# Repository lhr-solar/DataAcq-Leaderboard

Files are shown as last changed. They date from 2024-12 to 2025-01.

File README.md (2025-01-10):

# DataAcquisitionLeaderPCB

This PCB is designed for our solar vehicle to collect electrical and mechanical sensor data and transmit it wirelessly via LTE for real-time access. It also includes a GPS module for location tracking and an RF module as a backup communication system.

## LED Descriptions

LTE LEDs:

* HB (D7): Heartbeat.
  * Blinking = Our code is running on module.
* RSSI (D5): Received Singal Strength Integrity.
  * PWM based on strength (brighter = better).
* CONN (D4): Connection Indicator.
  * On, solid = Not connected.
  * 1/2 sec period blink = Last transmit failed.
  * 1 sec blink period = Normal operation.
* ON (D6): On.
  * On = Module is on.

RF LEDs:

* COM (D1): Commissioning (associate) status.
  * Blinking = Device is powered and operating properly.
  * Off = Device is alseep.
  * Note: blinks with certain patterns depending on number of RF_COM button presses (see datasheet).
* ON (D2): On.
  * On = Module is on.
* RSSI (D3): Received Singal Strength Integrity.
  * PWM based on strength (brighter = better).

GPS LED:

* NFX (D8): Negative 3D Fix.
  * Blinking (2 sec period) = Searching for satellites, no position fix.
  * Off = Acquired satellite signal.

## Testpoint Descriptions

LTE Testpoints:

* UART5 (J3)
  * Pin 3 TX = Transmit
  * Pin 2 RX = Receive
  * Pin 1 NR = Negative Reset (Note: this is not a UART singal, it is the module NRESET singal)

* Test Trace (J4)
  * Provides access to 4 pins (traces) to help in debugging code on the LTE module.

RF Testpoints:

* UART2 (J2)
  * Pin 3 TX = Transmit
  * Pin 2 RX = Receive
  * Pin 1 NR = Negative Reset (Note: this is not a UART singal, it is the module NRESET singal)

GPS Testpoints:

* I2C (J5)
  * Pin 3 SDA = Serial Data
  * Pin 2 SCL = Serial Clock
  * Pin 1 NR = Negative Reset (Note: this is not a I2C singal, it is the module NRESET singal)

## Pushbutton Descriptions

LTE_RESET: When pressed LTE module resets.
GPS_RESET: When pressed GPS module resets.
RF_RESET: When pressed RF module resets.
RF_COM: RF Commissioning button (see datasheet).

## PCB

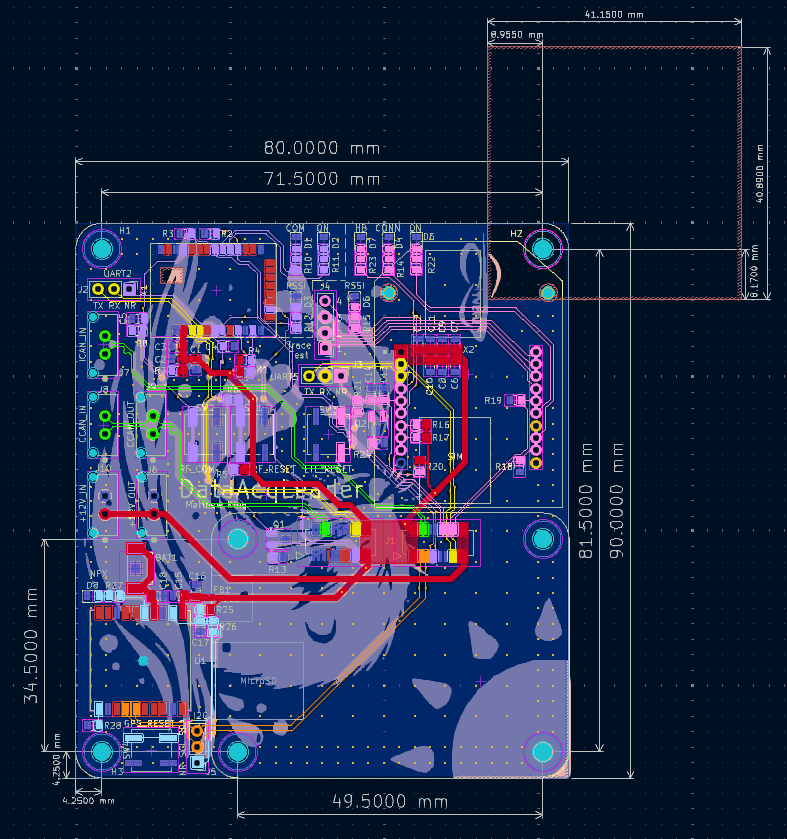
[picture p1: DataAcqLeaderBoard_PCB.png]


## Schematic

[PDF](DataAcqLeaderBoard_Schematic.pdf)

## BOM

[BOM](DataAcqLeaderBoard/bom/bom.csv)
[IBOM](DataAcqLeaderBoard/bom/ibom.html)
[Mouser Cart](https://www.mouser.com/ProjectManager/ProjectDetail.aspx?AccessID=583e28cb45)

Cart does not include: 

  - [GPS Ferite Bead](https://www.digikey.com/en/products/detail/pulse-electronics/GMLB-100505-0600A-N8/12417638)
  - [GPS Module]( https://www.adafruit.com/product/790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)
  - [Digi XBee LTE Module](https://www.digi.com/products/embedded-systems/digi-xbee/cellular-modems/digi-xbee-3-global-lte-cat-4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 )
  - [Digi XBee RF Module](https://www.digi.com/products/embedded-systems/digi-xbee/rf-modules/sub-1-ghz-rf-modules/digi-xbee-xr-900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)

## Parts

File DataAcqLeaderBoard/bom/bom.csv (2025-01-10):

# | Reference | Value | Qty | Footprint | Datasheet | P/N | Mouser Part Number | Link | DNP
1 | BAT1 | ML414 | 1 | DataAcqLeaderBoard-Footprints:BAT_2994TR | https://www.mouser.com/ProductDetail/Keystone-Electronics/2994TR?qs=BMR1h6ig6pBQGK4xQ7FwKQ%3D%3D | 2994TR | 534-2994TR | https://www.mouser.com/ProductDetail/Keystone-Electronics/2994TR?qs=BMR1h6ig6pBQGK4xQ7FwKQ%3D%3D
2 | C1,C9 | 10u | 2 | Capacitor_SMD:C_0805_2012Metric | ~ | TCP0J106M8R | 755-TCP0J106M8R | https://www.mouser.com/ProductDetail/KYOCERA-AVX/TCP0J106M8R?qs=gmcn8Ik9O3HZ%252B34S5YYCCQ%3D%3D
3 | C2,C4,C5,C14,C15,C17,C18 | 1u | 7 | Capacitor_SMD:C_0805_2012Metric | ~ | C0805C105J4RAC7210 | 80-C0805C105J4RACLR | https://www.mouser.com/ProductDetail/KEMET/C0805C105J4RAC7210?qs=7zB%252BIQS%2FKOJG%252BUtduyFhHw%3D%3D
4 | C3 | 47p | 1 | Capacitor_SMD:C_0805_2012Metric | ~ | C0805C470F5GACTU | 80-C0805C470F5G | https://www.mouser.com/ProductDetail/KEMET/C0805C470F5GACTU?qs=fI854BrZEijgUEI6lxo0jA%3D%3D
5 | C6,C7,C8 | 100u | 3 | Capacitor_SMD:C_0805_2012Metric | ~ | TCTPL0G107M8R-V1 | 755-TCTPL0G107M8R-V1 | https://www.mouser.com/ProductDetail/KYOCERA-AVX/TCTPL0G107M8R-V1?qs=Y0Uzf4wQF3nuA76NpVN8fA%3D%3D
6 | C10,C13 | 10n | 2 | Capacitor_SMD:C_0805_2012Metric | ~ | C0805C103F8HACAUTO | 80-C0805C103F8HAUTO | https://www.mouser.com/ProductDetail/KEMET/C0805C103F8HACAUTO?qs=j%252B1pi9TdxUbLXPjCpdS2Hw%3D%3D
7 | C11 | 56p | 1 | Capacitor_SMD:C_0805_2012Metric | ~ | C0805C560FBGACTU | 80-C0805C560FBG | https://www.mouser.com/ProductDetail/KEMET/C0805C560FBGACTU?qs=7IaIRco65pnJB5L%2Foom%252BKQ%3D%3D
8 | C12 | 10p | 1 | Capacitor_SMD:C_0805_2012Metric | ~ | C0805C100F1GACTU | 80-C0805C100F1GACTU | https://www.mouser.com/ProductDetail/KEMET/C0805C100F1GACTU?qs=sowatxGsQyzyczo0gS71EQ%3D%3D
9 | C16 | 100n | 1 | Capacitor_SMD:C_0805_2012Metric | ~ | C0805C104M5RACTU | 80-C0805C104M5R | https://www.mouser.com/ProductDetail/KEMET/C0805C104M5RACTU?qs=VOOUd%252Bza08qHu13WgNByHQ%3D%3D
10 | D1,D2,D3,D4,D5,D6,D7,D8 | -- mixed values -- | 8 | LED_SMD:LED_0805_2012Metric |  | APTD2012LCGCK | 604-APTD2012LCGCK | https://www.mouser.com/ProductDetail/Kingbright/APTD2012LCGCK?qs=AQlKX63v8RvNHN%2F9EGvNTg%3D%3D
11 | FB1 | FerriteBead | 1 | Resistor_SMD:R_0402_1005Metric | ~ | GMLB-100505-0600A-N8 |  | https://www.digikey.com/en/products/detail/pulse-electronics/GMLB-100505-0600A-N8/12417638
12 | H1,H2,H3,LOGO1,LOGO2,LOGO3 | -- mixed values -- | 6 | -- mixed values -- | -- mixed values --
13 | J1 | ~ | 1 | UTSVT_Special:LeaderSOM | https://www.molex.com/en-us/products/part-detail/533072471 | 53307-2471 | 538-53307-2471 | https://www.mouser.com/ProductDetail/Molex/53307-2471?qs=3DzawVMofg%252Bx9c%2FNm7UacA%3D%3D
14 | J2,J3,J5 | -- mixed values -- | 3 | Connector_PinHeader_2.54mm:PinHeader_1x03_P2.54mm_Vertical | ~ | 22-28-4035 | 538-22-28-4035 | https://www.mouser.com/ProductDetail/Molex/22-28-4035?qs=GAPJcf4kvduMvGzMBKHaPg%3D%3D
15 | J4 | LTE_Trace | 1 | Connector_PinHeader_2.54mm:PinHeader_1x04_P2.54mm_Vertical | ~ | 22-28-4045 | 538-22-28-4045 | https://www.mouser.com/ProductDetail/Molex/22-28-4045?qs=MuwpYaHj752m1cM4X%252BE7xA%3D%3D
16 | J6,J7,J8,J9,J10 | -- mixed values -- | 5 | DataAcqLeaderBoard-Footprints:CONN_SD-43650-006_02_MOL | ~ | 43650-0215 | 538-43650-0215 | https://www.mouser.com/ProductDetail/538-43650-0215
17 | Q1,Q2 | NMOS | 2 | Package_TO_SOT_SMD:SOT-23-3 | https://ngspice.sourceforge.io/docs/ngspice-html-manual/manual.xhtml#cha_MOSFETs | IRLML0030TRPBF | 942-IRLML0030TRPBF | https://www.mouser.com/ProductDetail/Infineon-Technologies/IRLML0030TRPBF?qs=9%252BKlkBgLFf0lLJi3xz1alg%3D%3D
18 | R1,R2,R3,R4,R5,R7,R13,R16,R17,R18,R19,R20,R24,R25,R28 | 10k | 15 | Resistor_SMD:R_0805_2012Metric | ~ | CRCW080510K0FKEA | 71-CRCW080510K0FKEAC | https://www.mouser.com/ProductDetail/Vishay-Dale/CRCW080510K0FKEA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
19 | R6,R8,R10,R11,R12,R14,R15,R21,R22,R23,R26,R27 | 1k | 12 | Resistor_SMD:R_0805_2012Metric | ~ | CRCW08051K00FKEAC | 71-CRCW08051K00FKEAC | https://www.mouser.com/ProductDetail/Vishay-Dale/CRCW08051K00FKEAC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
20 | SW1,SW2,SW3,SW4 | -- mixed values -- | 4 | Button_Switch_SMD:SW_SPST_B3SL-1002P | -- mixed values -- | B3SL-1002P | 653-B3SL-1002P | https://www.mouser.com/ProductDetail/Omron-Electronics/B3SL-1002P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
21 | U1 | PA1616S_GPS | 1 | DataAcqLeaderBoard-Footprints:PA1616S_ADA | https://cdn-shop.adafruit.com/product-files/746/CD+PA1616S+Datasheet.v03.pdf | PA1616S |  | https://www.adafruit.com/product/790?gad_source=1
22 | X1 | DigiXBeeRX900Micro | 1 | DataAcqLeaderBoard-Footprints:XBeeXR900RFMicro | https://fcc.report/FCC-ID/MCQ-XB9XR/7222310.pdf | XB-9XR-DMRM-001 |  | https://www.digi.com/products/embedded-systems/digi-xbee/rf-modules/sub-1-ghz-rf-modules/digi-xbee-xr-900
23 | X2 | DigiXBee3LTECat4 | 1 | DataAcqLeaderBoard-Footprints:DigiXBee3LTECat4 | https://www.digi.com/resources/documentation/digidocs/PDFs/90002503.pdf | XB3-C-G4-UT-001 |  | https://www.digi.com/products/embedded-systems/digi-xbee/cellular-modems/digi-xbee-3-global-lte-cat-4

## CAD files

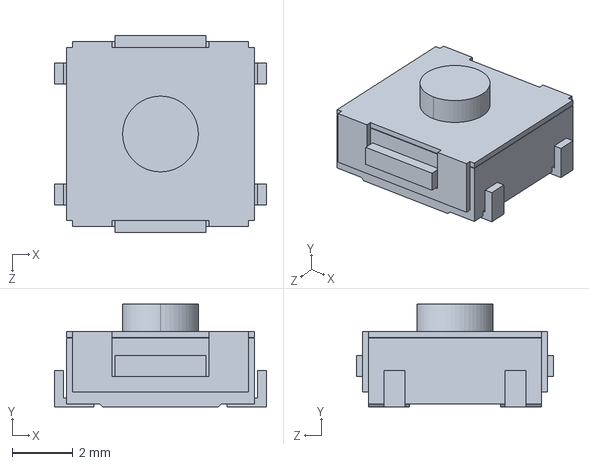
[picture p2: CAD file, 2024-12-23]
DataAcqLeaderBoard/3Dmodels/B3SL_100[]P.step
7.00 x 3.40 x 6.50 mm

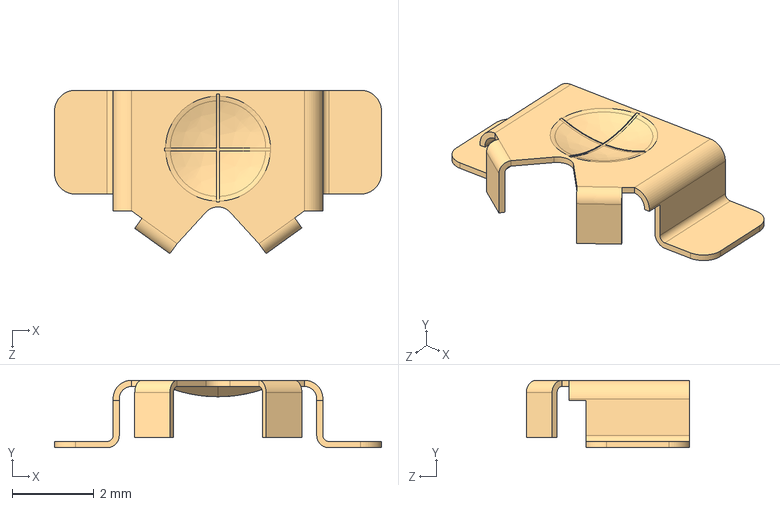
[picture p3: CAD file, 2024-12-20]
DataAcqLeaderBoard/3Dmodels/2994TR.step
8.00 x 1.65 x 4.00 mm

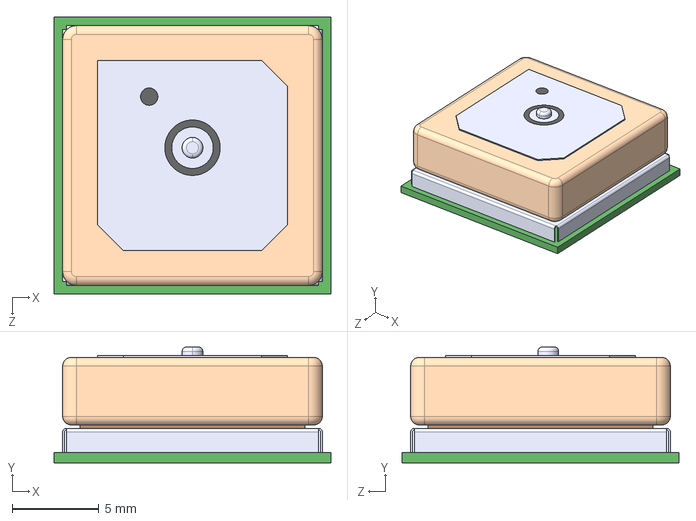
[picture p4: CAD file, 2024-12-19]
DataAcqLeaderBoard/3Dmodels/CD-PA1616D--3DModel-STEP-56544.STEP
16.0 x 6.70 x 16.0 mm

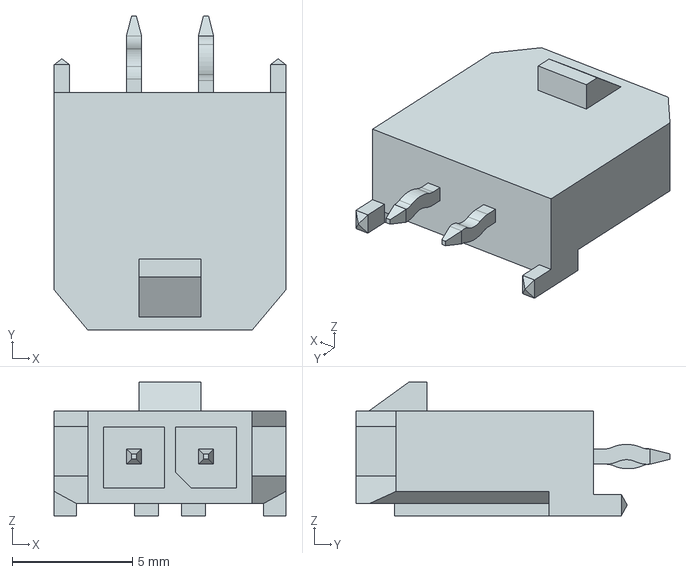
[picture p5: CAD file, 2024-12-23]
DataAcqLeaderBoard/3Dmodels/436500215.stp
9.65 x 13.1 x 5.57 mm

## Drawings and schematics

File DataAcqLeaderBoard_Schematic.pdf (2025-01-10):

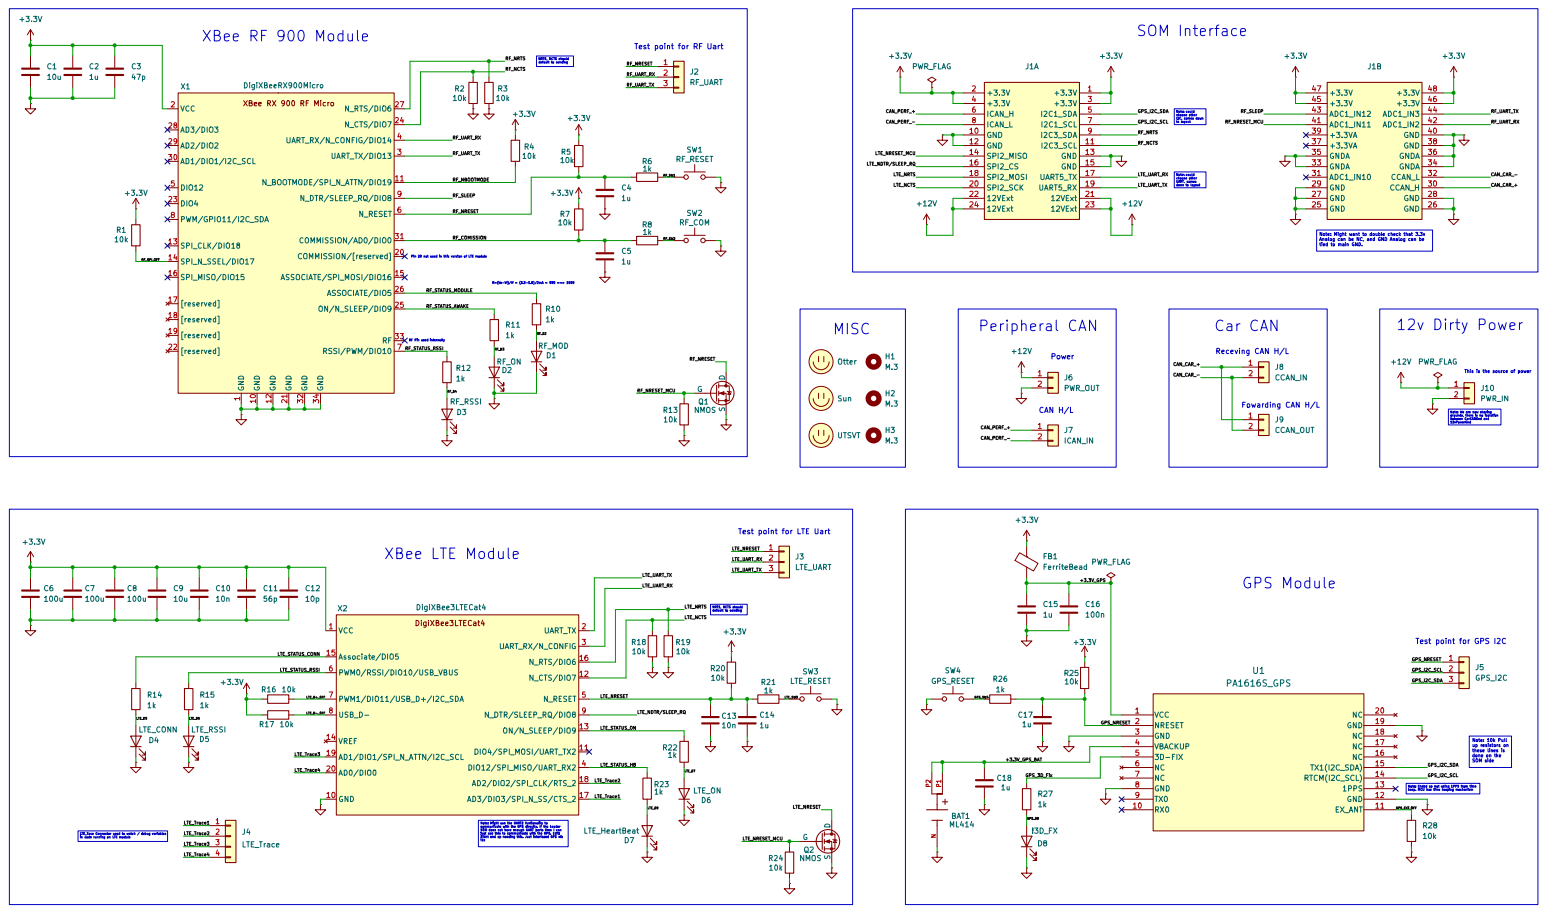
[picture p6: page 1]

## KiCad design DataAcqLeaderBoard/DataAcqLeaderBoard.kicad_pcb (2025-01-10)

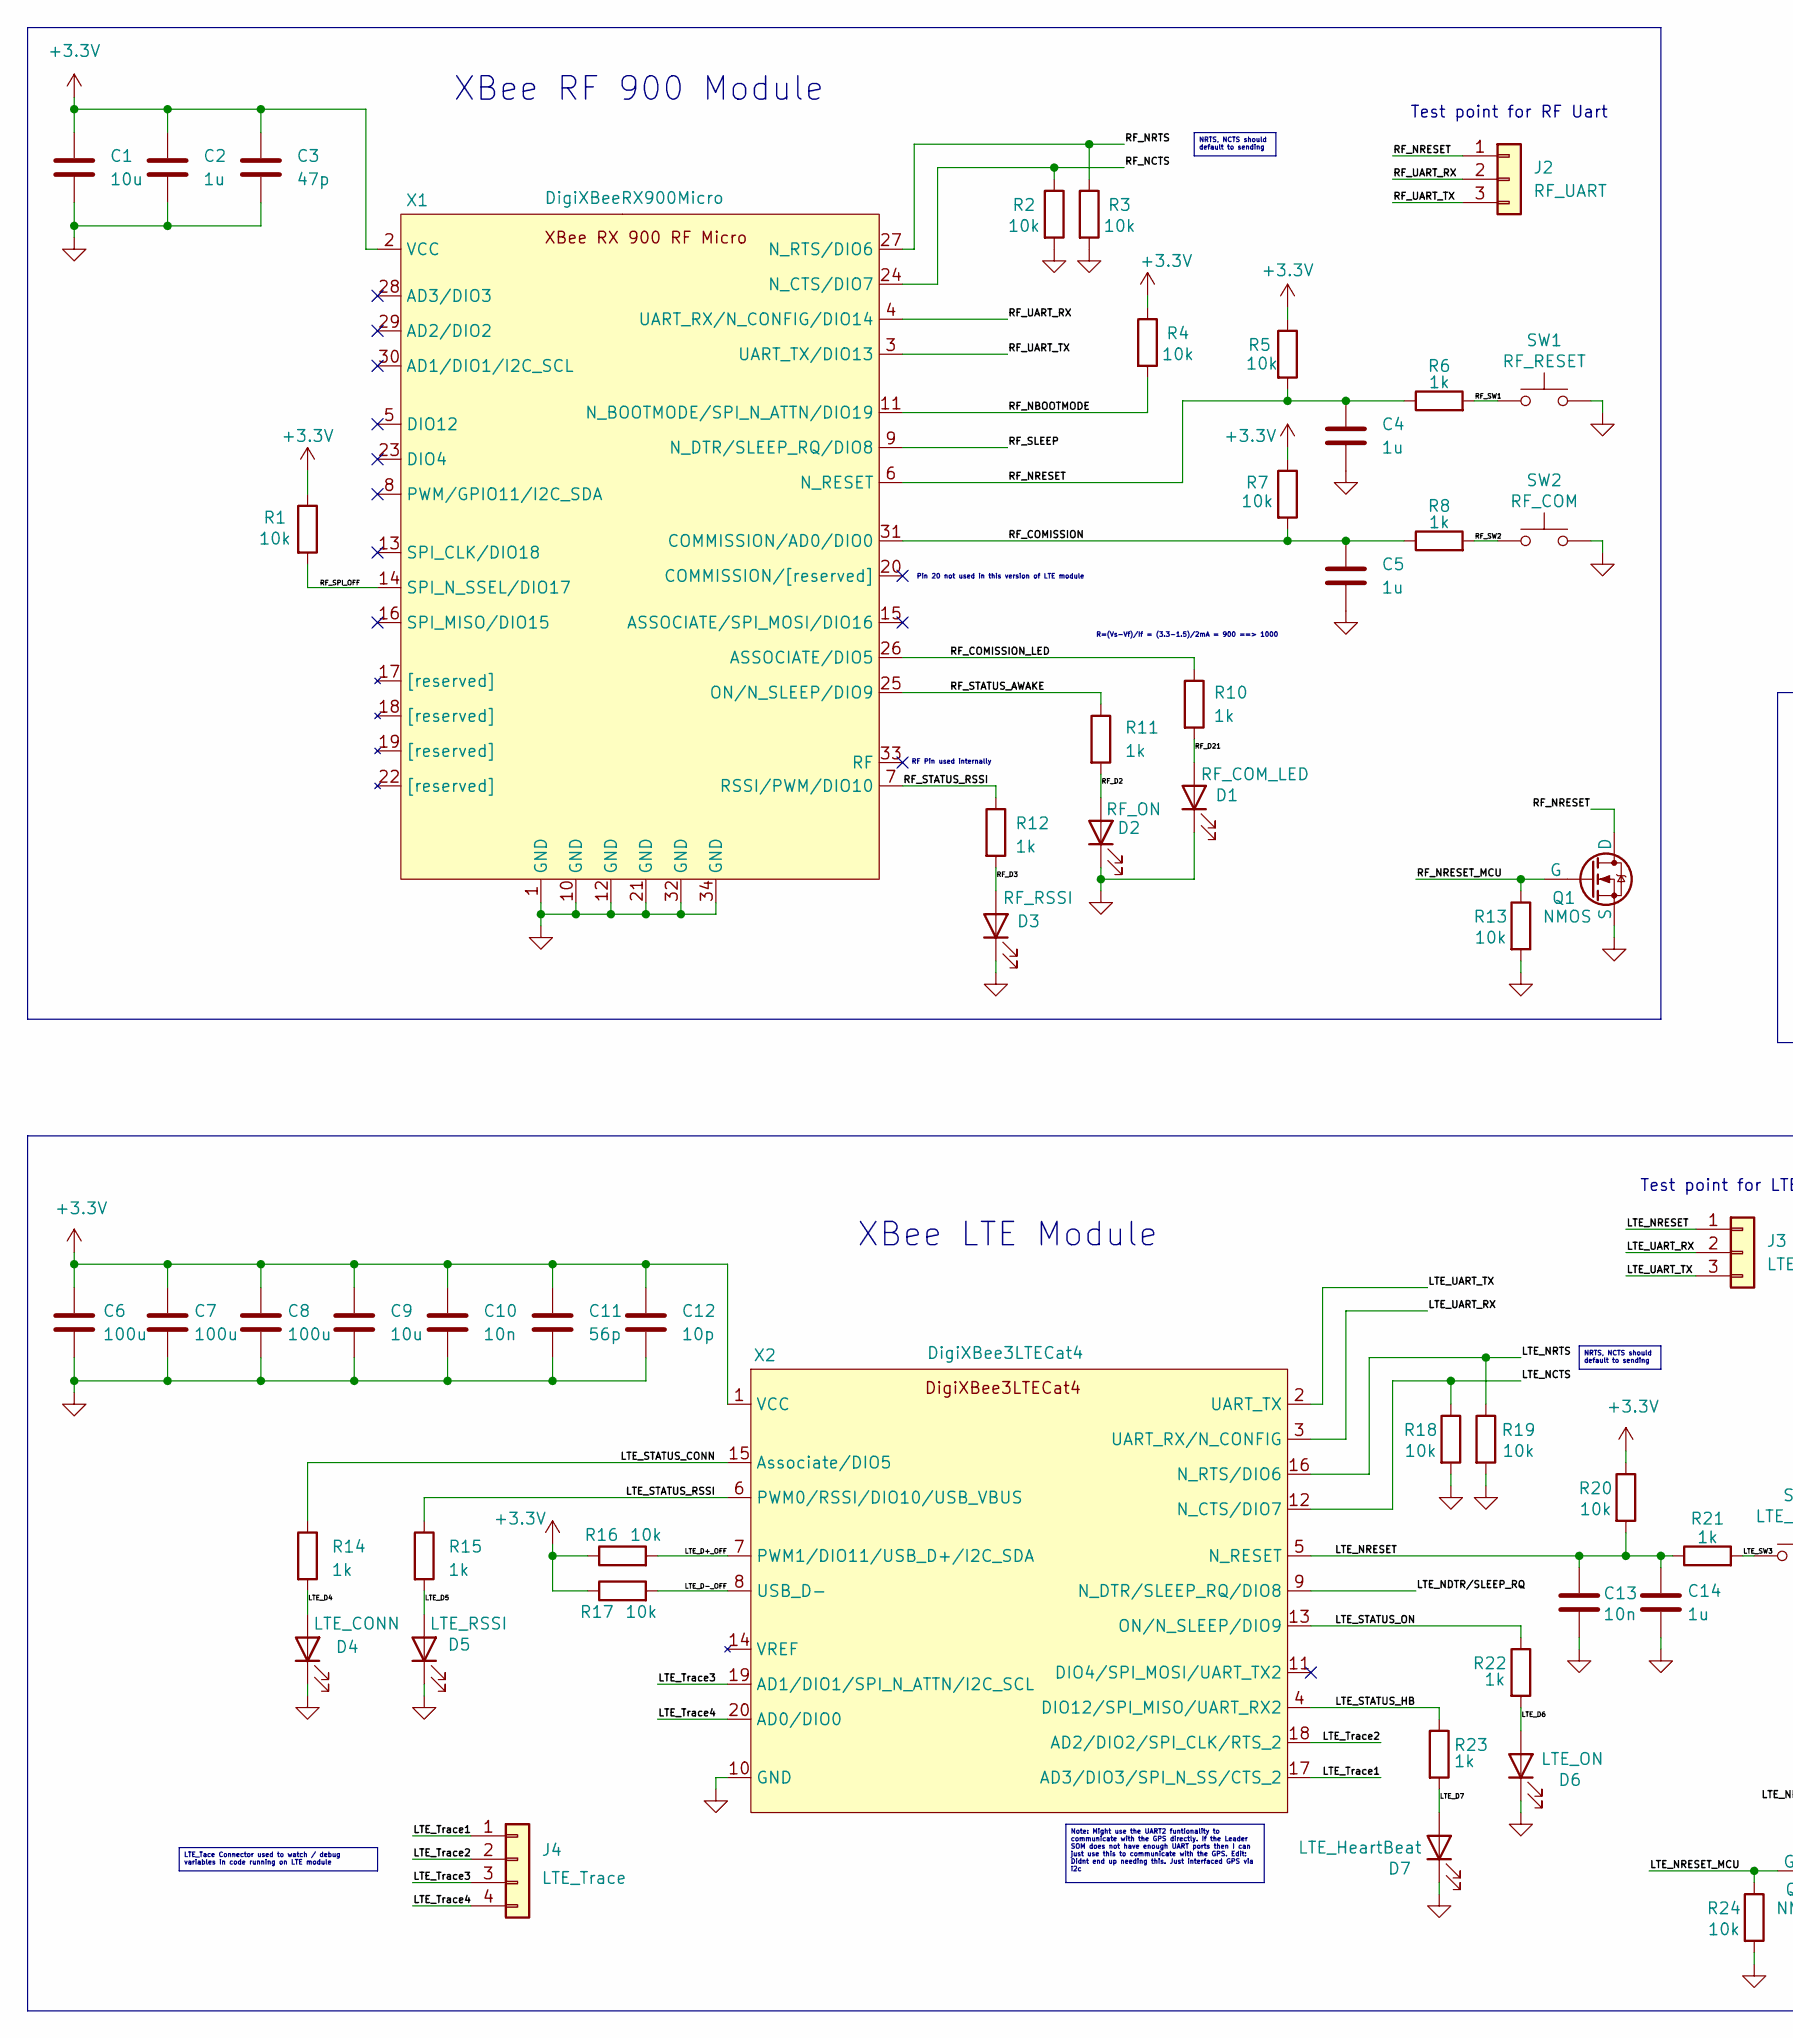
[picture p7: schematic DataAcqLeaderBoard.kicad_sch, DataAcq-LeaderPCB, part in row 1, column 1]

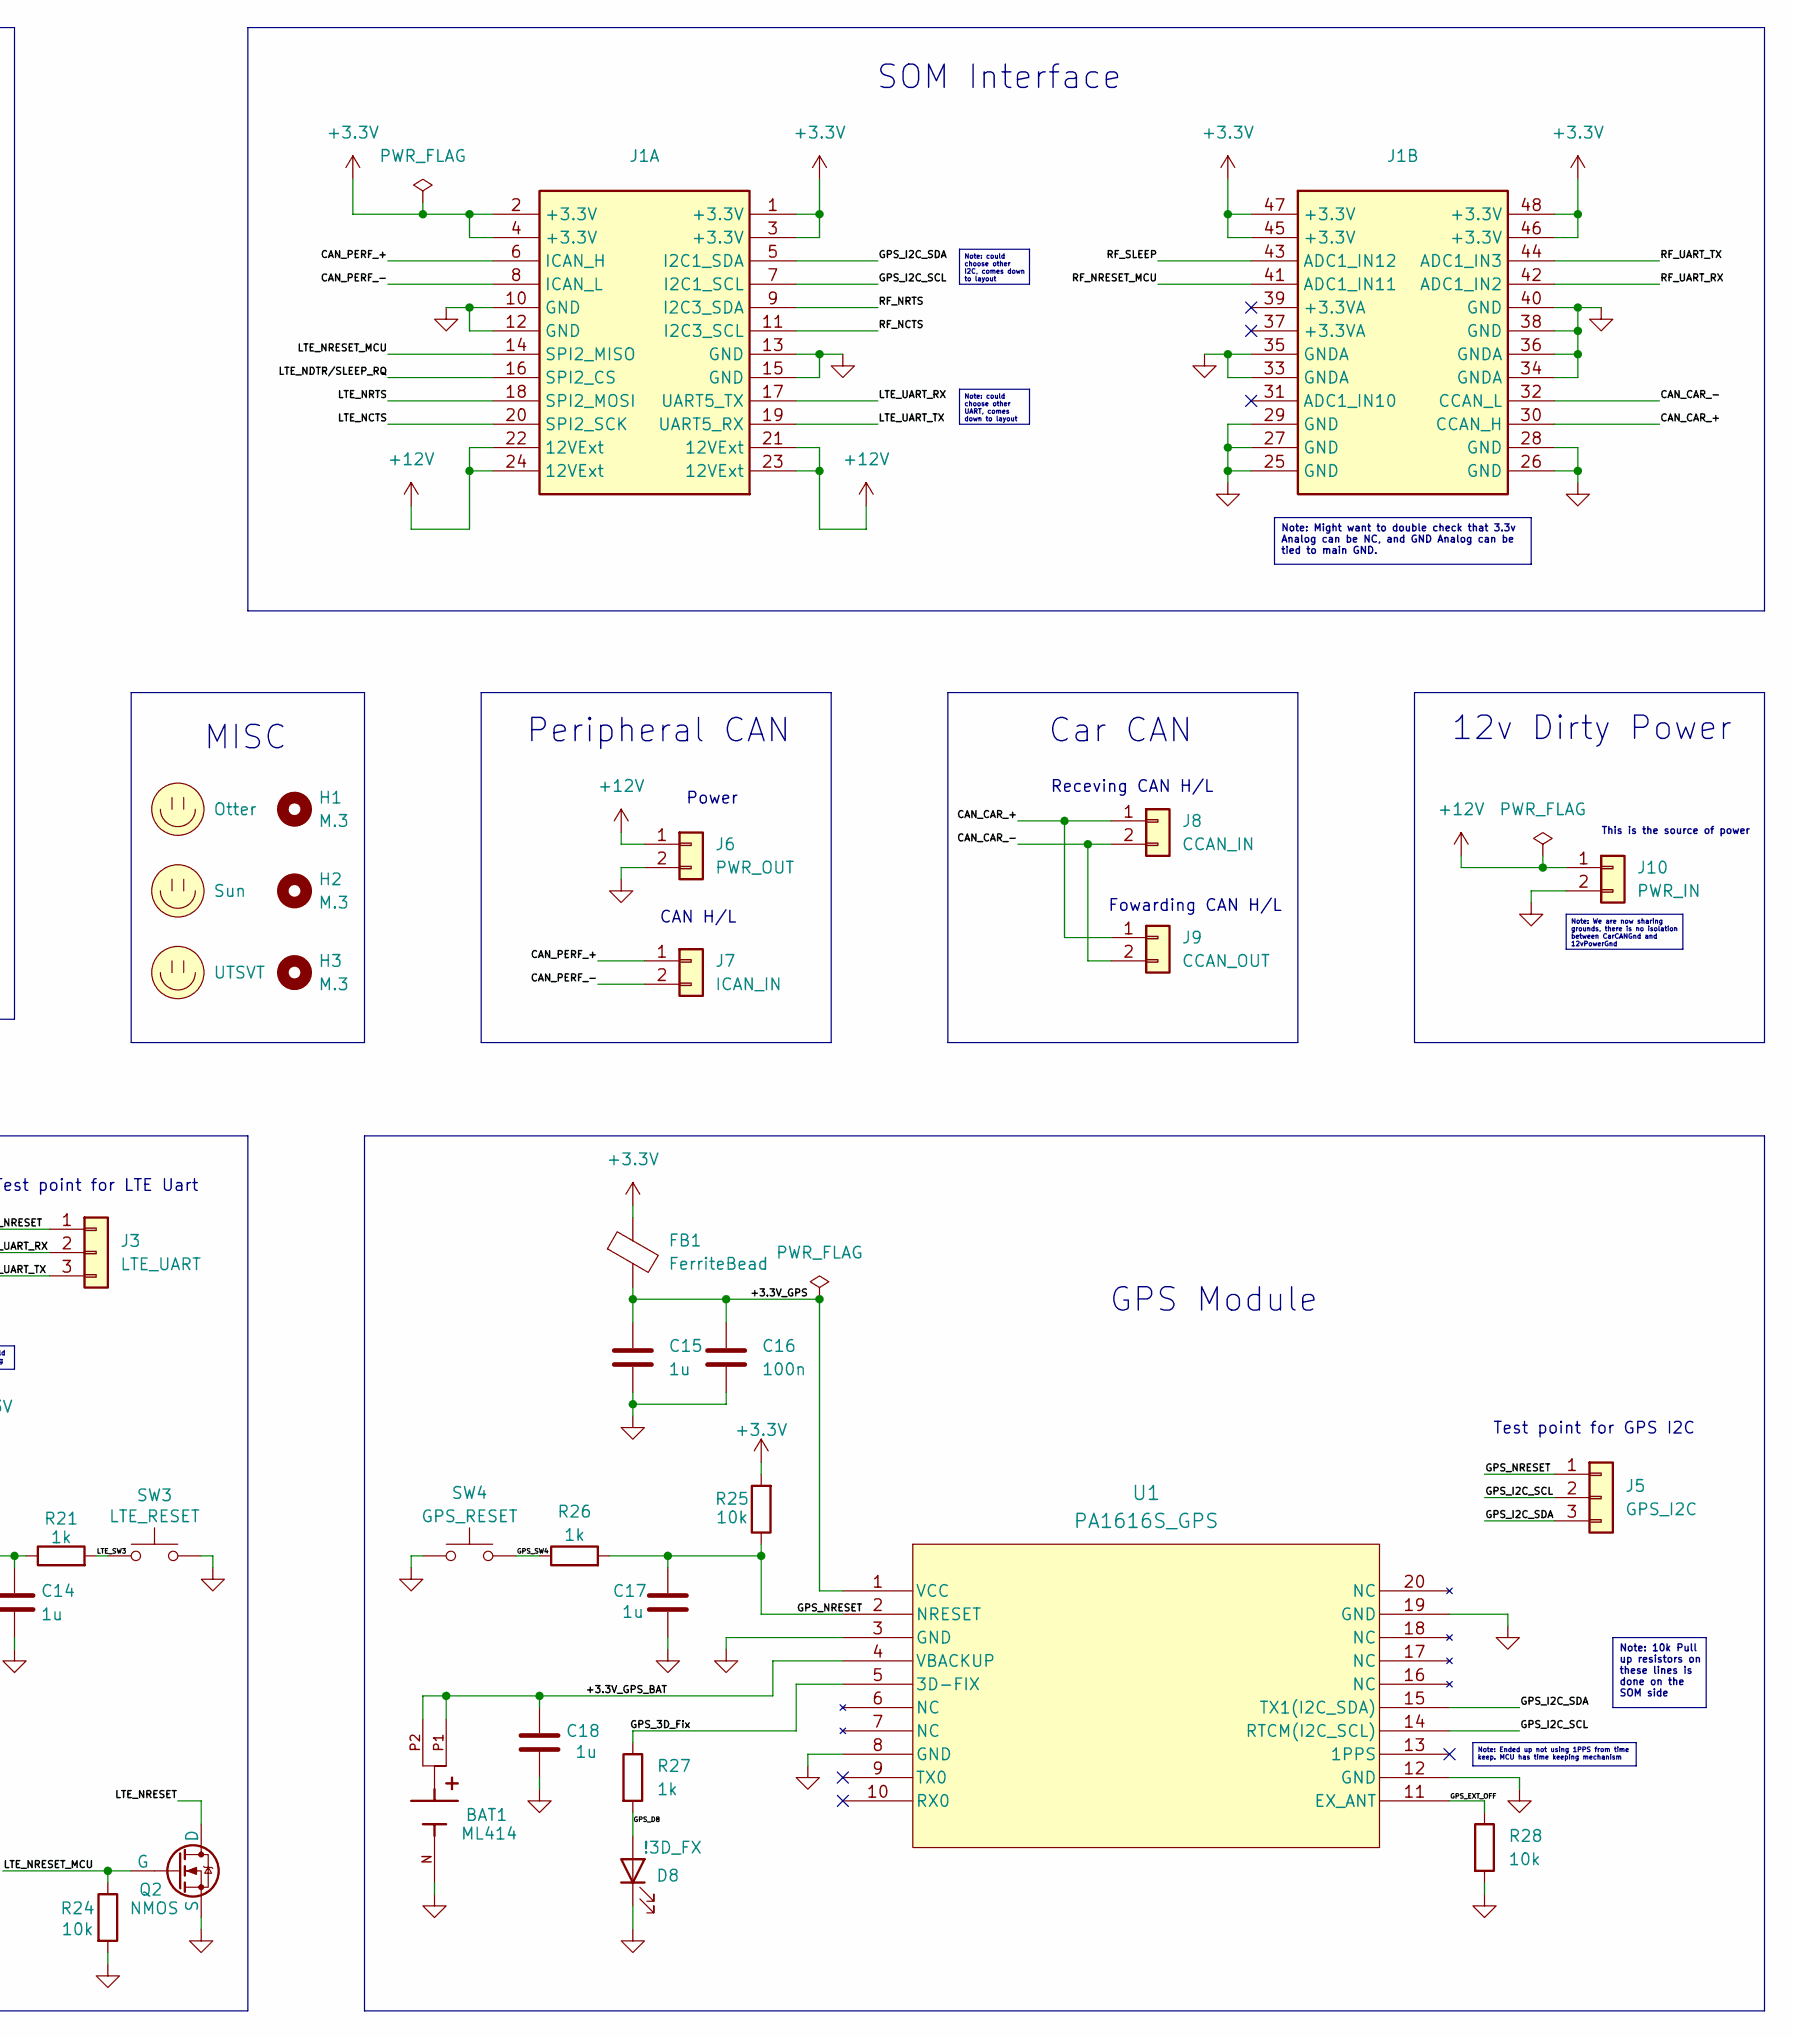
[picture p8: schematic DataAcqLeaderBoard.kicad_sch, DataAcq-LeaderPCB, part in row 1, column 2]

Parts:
BAT1: ML414; BAT_2994TR; Mouser Part Number 534-2994TR
C1, C9: 10u; C_0805_2012Metric; Mouser Part Number 755-TCP0J106M8R
C2, C4, C5, C14, C15, C17, C18: 1u; C_0805_2012Metric; Mouser Part Number 80-C0805C105J4RACLR
C3: 47p; C_0805_2012Metric; Mouser Part Number 80-C0805C470F5G
C6, C7, C8: 100u; C_0805_2012Metric; Mouser Part Number 755-TCTPL0G107M8R-V1
C10, C13: 10n; C_0805_2012Metric; Mouser Part Number 80-C0805C103F8HAUTO
C11: 56p; C_0805_2012Metric; Mouser Part Number 80-C0805C560FBG
C12: 10p; C_0805_2012Metric; Mouser Part Number 80-C0805C100F1GACTU
C16: 100n; C_0805_2012Metric; Mouser Part Number 80-C0805C104M5R
D1: RF_COM_LED; LED_0805_2012Metric; Mouser Part Number 604-APTD2012LCGCK
D2: RF_ON; LED_0805_2012Metric; Mouser Part Number 604-APTD2012LCGCK
D3: RF_RSSI; LED_0805_2012Metric; Mouser Part Number 604-APTD2012LCGCK
D4: LTE_CONN; LED_0805_2012Metric; Mouser Part Number 604-APTD2012LCGCK
D5: LTE_RSSI; LED_0805_2012Metric; Mouser Part Number 604-APTD2012LCGCK
D6: LTE_ON; LED_0805_2012Metric; Mouser Part Number 604-APTD2012LCGCK
D7: LTE_HeartBeat; LED_0805_2012Metric; Mouser Part Number 604-APTD2012LCGCK
D8: !3D_FX; LED_0805_2012Metric; Mouser Part Number 604-APTD2012LCGCK
FB1: FerriteBead; R_0402_1005Metric
H1, H2, H3: M.3; MountingHole_3mm
J1: LeaderSOM; Mouser Part Number 538-53307-2471
J2: RF_UART; PinHeader_1x03_P2.54mm_Vertical; Mouser Part Number 538-22-28-4035
J3: LTE_UART; PinHeader_1x03_P2.54mm_Vertical; Mouser Part Number 538-22-28-4035
J4: LTE_Trace; PinHeader_1x04_P2.54mm_Vertical; Mouser Part Number 538-22-28-4045
J5: GPS_I2C; PinHeader_1x03_P2.54mm_Vertical; Mouser Part Number 538-22-28-4035
J6: PWR_OUT; CONN_SD-43650-006_02_MOL; Mouser Part Number 538-43650-0215
J7: ICAN_IN; CONN_SD-43650-006_02_MOL; Mouser Part Number 538-43650-0215
J8: CCAN_IN; CONN_SD-43650-006_02_MOL; Mouser Part Number 538-43650-0215
J9: CCAN_OUT; CONN_SD-43650-006_02_MOL; Mouser Part Number 538-43650-0215
J10: PWR_IN; CONN_SD-43650-006_02_MOL; Mouser Part Number 538-43650-0215
LOGO1: Otter; otter
LOGO2: UTSVT; UTSVT_Logo_Symbol
LOGO3: Sun; sun
Q1, Q2: NMOS; SOT-23-3; Mouser Part Number 942-IRLML0030TRPBF
R1, R2, R3, R4, R5, R7, R13, R16, R17, R18, R19, R20, R24, R25, R28: 10k; R_0805_2012Metric; Mouser Part Number 71-CRCW080510K0FKEAC
R6, R8, R10, R11, R12, R14, R15, R21, R22, R23, R26, R27: 1k; R_0805_2012Metric; Mouser Part Number 71-CRCW08051K00FKEAC
SW1: RF_RESET; SW_SPST_B3SL-1002P; Mouser Part Number 653-B3SL-1002P
SW2: RF_COM; SW_SPST_B3SL-1002P; Mouser Part Number 653-B3SL-1002P
SW3: LTE_RESET; SW_SPST_B3SL-1002P; Mouser Part Number 653-B3SL-1002P
SW4: GPS_RESET; SW_SPST_B3SL-1002P; Mouser Part Number 653-B3SL-1002P
U1: PA1616S_GPS; PA1616S_ADA
X1: DigiXBeeRX900Micro; XBeeXR900RFMicro
X2: DigiXBee3LTECat4

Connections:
+3.3V: C1.1, C2.1, C3.1, C6.1, C7.1, C8.1, C9.1, C10.1, C11.1, C12.1, FB1.1, J1.1 (+3.3V), J1.2 (+3.3V), J1.3 (+3.3V), J1.4 (+3.3V), J1.45 (+3.3V), J1.46 (+3.3V), J1.47 (+3.3V), J1.48 (+3.3V), R1.1, R4.1, R5.1, R7.1, R16.1, R17.1, R20.1, R25.2, X1.2 (VCC), X2.1 (VCC)
+12V: J1.21 (12VExt), J1.22 (12VExt), J1.23 (12VExt), J1.24 (12VExt), J6.1, J10.1
/+3.3V_GPS: C15.1, C16.1, FB1.2, U1.1 (VCC)
/+3.3V_GPS_BAT: BAT1.P1, BAT1.P2, C18.1, U1.4 (VBACKUP)
/CAN_CAR_+: J1.30 (CCAN_H), J8.1, J9.1
/CAN_CAR_-: J1.32 (CCAN_L), J8.2, J9.2
/CAN_PERF_+: J1.6 (ICAN_H), J7.1
/CAN_PERF_-: J1.8 (ICAN_L), J7.2
/GPS_3D_Fix: R27.1, U1.5 (3D-FIX)
/GPS_D8: D8.2 (A), R27.2
/GPS_EXT_OFF: R28.1, U1.11 (EX_ANT)
/GPS_I2C_SCL: J1.7 (I2C1_SCL), J5.2, U1.14 (RTCM(I2C_SCL))
/GPS_I2C_SDA: J1.5 (I2C1_SDA), J5.3, U1.15 (TX1(I2C_SDA))
/GPS_NRESET: C17.1, J5.1, R25.1, R26.2, U1.2 (NRESET)
/GPS_SW4: R26.1, SW4.2
/LTE_D4: D4.2 (A), R14.2
/LTE_D5: D5.2 (A), R15.2
/LTE_D6: D6.2 (A), R22.2
/LTE_D7: D7.2 (A), R23.2
/LTE_D+_OFF: R16.2, X2.7 (PWM1/DIO11/USB_D+/I2C_SDA)
/LTE_D-_OFF: R17.2, X2.8 (USB_D-)
/LTE_NCTS: J1.20 (SPI2_SCK), R18.1, X2.12 (N_CTS/DIO7)
/LTE_NDTR/SLEEP_RQ: J1.16 (SPI2_CS), X2.9 (N_DTR/SLEEP_RQ/DIO8)
/LTE_NRESET: C13.1, C14.1, J3.1, Q2.1 (D), R20.2, R21.1, X2.5 (N_RESET)
/LTE_NRESET_MCU: J1.14 (SPI2_MISO), Q2.2 (G), R24.1
/LTE_NRTS: J1.18 (SPI2_MOSI), R19.1, X2.16 (N_RTS/DIO6)
/LTE_STATUS_CONN: R14.1, X2.15 (Associate/DIO5)
/LTE_STATUS_HB: R23.1, X2.4 (DIO12/SPI_MISO/UART_RX2)
/LTE_STATUS_ON: R22.1, X2.13 (ON/N_SLEEP/DIO9)
/LTE_STATUS_RSSI: R15.1, X2.6 (PWM0/RSSI/DIO10/USB_VBUS)
/LTE_SW3: R21.2, SW3.1
/LTE_Trace1: J4.1, X2.17 (AD3/DIO3/SPI_N_SS/CTS_2)
/LTE_Trace2: J4.2, X2.18 (AD2/DIO2/SPI_CLK/RTS_2)
/LTE_Trace3: J4.3, X2.19 (AD1/DIO1/SPI_N_ATTN/I2C_SCL)
/LTE_Trace4: J4.4, X2.20 (AD0/DIO0)
/LTE_UART_RX: J1.17 (UART5_TX), J3.2, X2.3 (UART_RX/N_CONFIG)
/LTE_UART_TX: J1.19 (UART5_RX), J3.3, X2.2 (UART_TX)
/RF_COMISSION: C5.1, R7.2, R8.1, X1.31 (COMMISSION/AD0/DIO0)
/RF_COMISSION_LED: R10.1, X1.26 (ASSOCIATE/DIO5)
/RF_D2: D2.2 (A), R11.2
/RF_D3: D3.2 (A), R12.2
/RF_D21: D1.2 (A), R10.2
/RF_NBOOTMODE: R4.2, X1.11 (N_BOOTMODE/SPI_N_ATTN/DIO19)
/RF_NCTS: J1.11 (I2C3_SCL), R2.1, X1.24 (N_CTS/DIO7)
/RF_NRESET: C4.1, J2.1, Q1.1 (D), R5.2, R6.1, X1.6 (N_RESET)
/RF_NRESET_MCU: J1.41 (ADC1_IN11), Q1.2 (G), R13.1
/RF_NRTS: J1.9 (I2C3_SDA), R3.1, X1.27 (N_RTS/DIO6)
/RF_SLEEP: J1.43 (ADC1_IN12), X1.9 (N_DTR/SLEEP_RQ/DIO8)
/RF_SPI_OFF: R1.2, X1.14 (SPI_N_SSEL/DIO17)
/RF_STATUS_AWAKE: R11.1, X1.25 (ON/N_SLEEP/DIO9)
/RF_STATUS_RSSI: R12.1, X1.7 (RSSI/PWM/DIO10)
/RF_SW1: R6.2, SW1.1
/RF_SW2: R8.2, SW2.1
/RF_UART_RX: J1.42 (ADC1_IN2), J2.2, X1.4 (UART_RX/N_CONFIG/DIO14)
/RF_UART_TX: J1.44 (ADC1_IN3), J2.3, X1.3 (UART_TX/DIO13)
GND: BAT1.N, C1.2, C2.2, C3.2, C4.2, C5.2, C6.2, C7.2, C8.2, C9.2, C10.2, C11.2, C12.2, C13.2, C14.2, C15.2, C16.2, C17.2, C18.2, D1.1 (K), D2.1 (K), D3.1 (K), D4.1 (K), D5.1 (K), D6.1 (K), D7.1 (K), D8.1 (K), J1.10 (GND), J1.12 (GND), J1.13 (GND), J1.15 (GND), J1.25 (GND), J1.26 (GND), J1.27 (GND), J1.28 (GND), J1.29 (GND), J1.33 (GNDA), J1.34 (GNDA), J1.35 (GNDA), J1.36 (GNDA), J1.38 (GND), J1.40 (GND), J6.2, J10.2, Q1.3 (S), Q2.3 (S), R2.2, R3.2, R13.2, R18.2, R19.2, R24.2, R28.2, SW1.2, SW2.2, SW3.2, SW4.1, U1.3 (GND), U1.8 (GND), U1.12 (GND), U1.19 (GND), X1.1 (GND), X1.10 (GND), X1.12 (GND), X1.21 (GND), X1.32 (GND), X1.34 (GND), X2.10 (GND)

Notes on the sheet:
NRTS, NCTS should default to sending
Note: could choose other UART, comes down to layout
Note: Might want to double check that 3.3v Analog can be NC, and GND Analog can be tied to main GND.
Note: 10k Pull up resistors on these lines is done on the SOM side
LTE_Tace Connector used to watch / debug variables in code running on LTE module
Note: Ended up not using 1PPS from time keep. MCU has time keeping mechanism
Note: We are now sharing grounds, there is no isolation between CarCANGnd and 12vPowerGnd
Note: could choose other I2C, comes down to layout
Note: Might use the UART2 funtionality to communicate with the GPS directly. If the Leader SOM does not have enough UART ports then I can just use this to communicate with the GPS. Edit: Didnt end up needing this. Just interfaced GPS via i2c
Test point for LTE Uart
This is the source of power
Test point for RF Uart
Pin 20 not used in this version of LTE module
XBee LTE Module
12v Dirty Power
Receving CAN H/L
Test point for GPS I2C
MISC
Car CAN
GPS Module
CAN H/L
RF Pin used internally
Fowarding CAN H/L
XBee RF 900 Module
R=(Vs-Vf)/If = (3.3-1.5)/2mA = 900 ==> 1000
Power
Peripheral CAN
SOM Interface

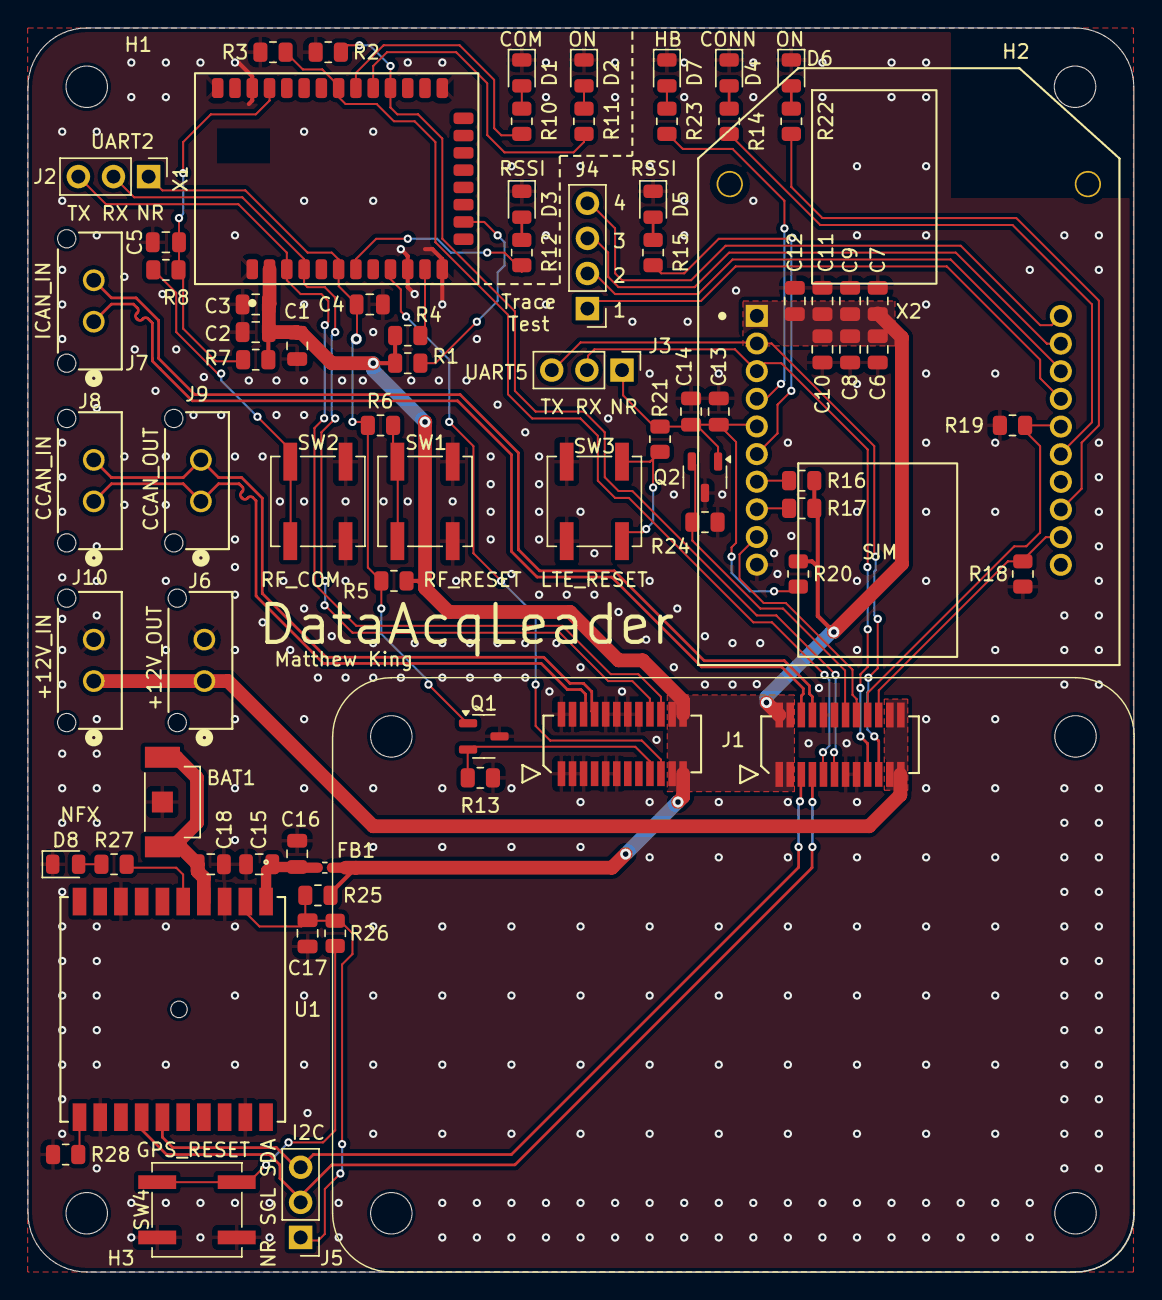
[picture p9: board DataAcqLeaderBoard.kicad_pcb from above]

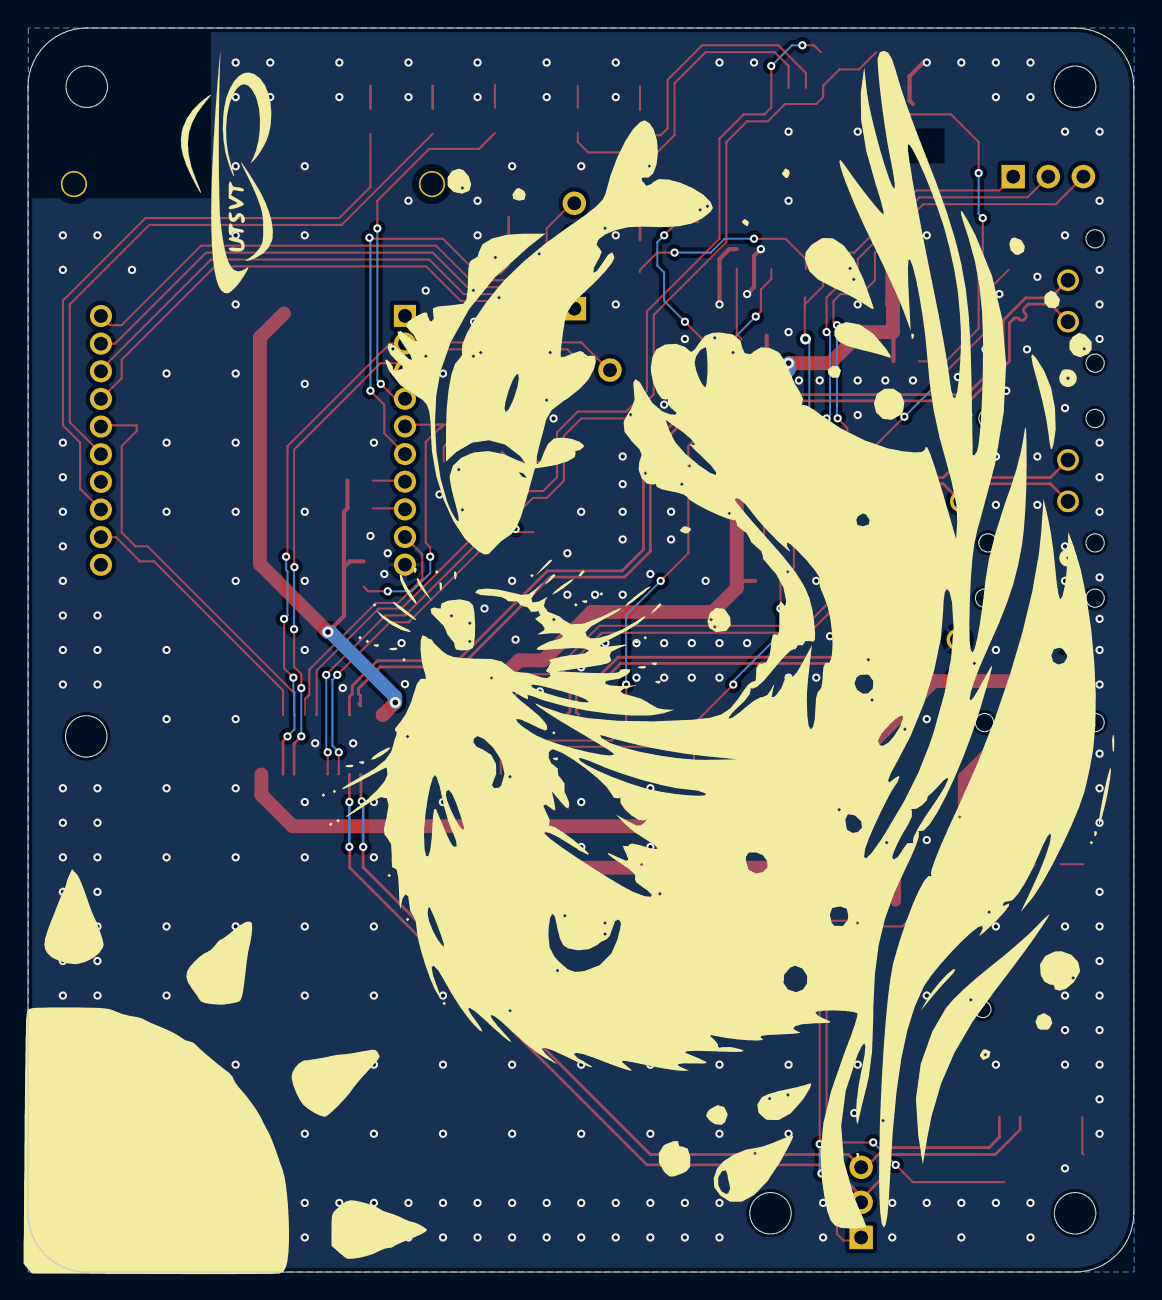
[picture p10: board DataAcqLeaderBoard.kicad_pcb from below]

Board: 2 copper layers, 80.0 x 90.0 mm, 80 parts (3 on the bottom side), 56 nets.

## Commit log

2024-11-09 Inital comit
    [DataAcqLeaderBoard.kicad_pcb, DataAcqLeaderBoard.kicad_sch]
2024-11-09 Added GPS
    [DataAcqLeaderBoard.kicad_sch]
2024-11-17 Added XBee RF Module
    [DataAcqLeaderBoard.kicad_sch]
2024-11-18 Fixed RF Module's push buttons
    [DataAcqLeaderBoard.kicad_sch]
2024-11-23 Fixed project paths and added .gitignore
    [DataAcqLeaderBoard.kicad_pcb, DataAcqLeaderBoard.kicad_sch]
2024-11-26 Actually fixed the symbol, footprint paths
    [DataAcqLeaderBoard.kicad_sch]
2024-11-26 Removed old junk (symbol, footprint file setup)
    [DataAcqLeaderBoard.kicad_pcb]
2024-11-27 Added Digi XBee LTE Module
    [DataAcqLeaderBoard.kicad_pcb, DataAcqLeaderBoard.kicad_sch]
2024-11-27 Debounced Push Buttons
    [DataAcqLeaderBoard.kicad_sch]
2024-12-17 Added XBee RF and LTE Footprints
    [DataAcqLeaderBoard.kicad_pcb, DataAcqLeaderBoard.kicad_sch]
2024-12-19 Interfaced Leader SOM and added UTSVT Library
    [CD-PA1616D--3DModel-STEP-56544.STEP, DataAcqLeaderBoard.kicad_pcb, DataAcqLeaderBoard.kicad_sch]
2024-12-20 First revision of schematic done
    [2994TR.step, DataAcqLeaderBoard.kicad_pcb, DataAcqLeaderBoard.kicad_sch]
2024-12-23 Completed first draft of layout
    [436500215.stp, B3SL_100[]P.step, DataAcqLeaderBoard.kicad_pcb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]
2025-01-03 Updated Schematic, finished first rev of Layout
    [DataAcqLeaderBoard.kicad_pcb, DataAcqLeaderBoard.kicad_sch]
2025-01-06 Added README, added PCB dimensions
    [DataAcqLeaderBoard.kicad_pcb]
2025-01-10 Completed BOM & Filled out PR template
    [DataAcqLeaderBoard.kicad_pcb, DataAcqLeaderBoard.kicad_sch, bom.csv]
